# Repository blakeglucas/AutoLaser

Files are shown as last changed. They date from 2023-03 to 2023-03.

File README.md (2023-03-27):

# Auto Laser

An automatic laser pointer mover for your cat!

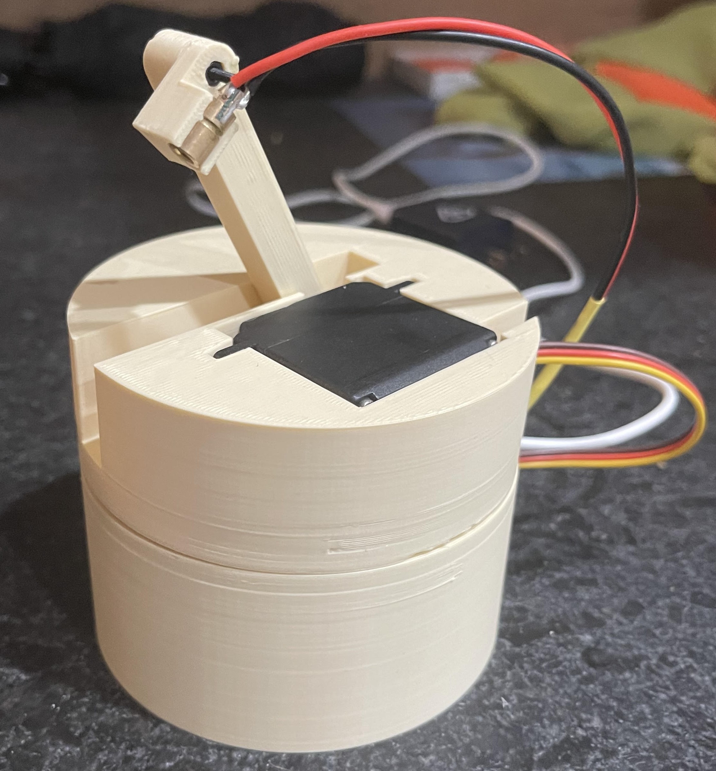
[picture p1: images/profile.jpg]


## Folders

### 3D

This folder contains the STL files for 3D printing and the FreeCAD source files for easy modification. Not every FreeCAD file has an associated STL because some are used as building blocks rather than as separate parts.

### Firmware

This folder contains the MicroPython firmware. This project was initially designed for the Pi Pico W, and the BaseMount part includes a corresponding mount, but you could modify it for use with another MicroPython compatible board (or just write your own firmware).

### PCB

This folder contains the design files for a Pi Pico (W) hat that makes connecting the laser and motors to the Pi Pico much easier. This part is not required.

## BOM

| Quantity | Part |
| ---| --- |
| 2 | TowerPro SG-5010 (or body-compatible) servo motors |
| 1 | Pi Pico W |
| 4 | M3x8 bolts |
| 4 | M3 nuts |
| 5 | M2x8 bolts |
| 5 | M2 nuts |
| 1 | Laser diode module |
| 2 | Longer wires for the laser module |
| 1 | Micro-USB cable and wall plug |
| Any | Cat |

> Servos: https://www.adafruit.com/product/155

> Laser Diodes: https://www.amazon.com/gp/product/B088PQQ9XV/

## Instructions

> If using a Pi Pico (W), be sure to flash MicroPython before starting. https://micropython.org/download/rp2-pico/

1. 3D print the STL files in the `3D` folder. Print plenty of extras of `ServoShaft` and `LaserArm`.
1. Connect your Pi Pico (W) to your computer and copy the Python files in the `Firmware` folder to your board, either via [Thonny](https://thonny.org/), [mpremote](https://docs.micropython.org/en/latest/reference/mpremote.html), or another way if you know one. After copying the files, disconnect your board from the computer.
1. (If using the PicoHat PCB) Solder the PicoHat to your Pi Pico (W).
1. Disassemble your servos and replace each drive shaft with the printed `ServoShaft` piece. It should be a drop-in replacement. Reassemble.
1. Attach the Pi Pico (W) to the `BaseMount` part using four of the M2 bolts and nuts. If you're using the PicoHat PCB, it's tricky to get the two by the micro-USB port, but it is doable.
1. Attach one of the servos to the `BaseMount` part using the M3 bolts and nuts.
1. (If necessary) De-solder the stock wires from the module and solder on two longer wires.
1. Snap the laser diode module into the `LaserHolder` part.
1. Attach the `LaserHolder` part to the `LaserArm` part using the remaining M2 bolt and nut.
1. Slide the `LaserArm` part onto the free servo's shaft at as close to a 90 degree angle as you can get.
1. Insert the free servo with the `LaserArm` attached into the `YMount` part.
1. Attach the now-assembled `YMount` part to `BaseMount`.
1. Slide the servo and laser wires through the slit on the back of `BaseMount` and attach them to your Pi Pico (W), either via the provided PicoHat or another method.
1. Connect your board to a power source. The servos will be driven to the zero position (50% duty), pause for five seconds, then begin the random laser movement.

## 3D Printing Instructions

> If you haven't tried the "Lightning" fill pattern in PrusaSlicer/SuperSlicer, give it a shot.

### BaseMount

Print top-face-down, using supports for only the counterbore screw holes on the face. Any infill, any layer height (0.2mm recommended).

### LaserArm

Print with the gear attachment hole facing up. Use support for only the counterbore screw hole. Sparse infill is fine, any layer height (18% and 0.2mm recommended, respectively).

### LaserHolder

Print the obvious orientation. No supports required. A finer layer height could be beneficial, but 0.2mm will work just fine.

### ServoShaft

If you have a printer with a 0.2-0.25mm nozzle, that is preferable, but a 0.4mm nozzle will work too. Add a support enforcer for the large negative area inside the gear, but support is not required for inside the smaller hole. 0.2mm layer height recommended, 100% infill for strength.

### YMount

Print the obvious orientation. Use support for the inset hole but not for inside the gear hole. Sparse infill, 0.2mm layer height recommended.

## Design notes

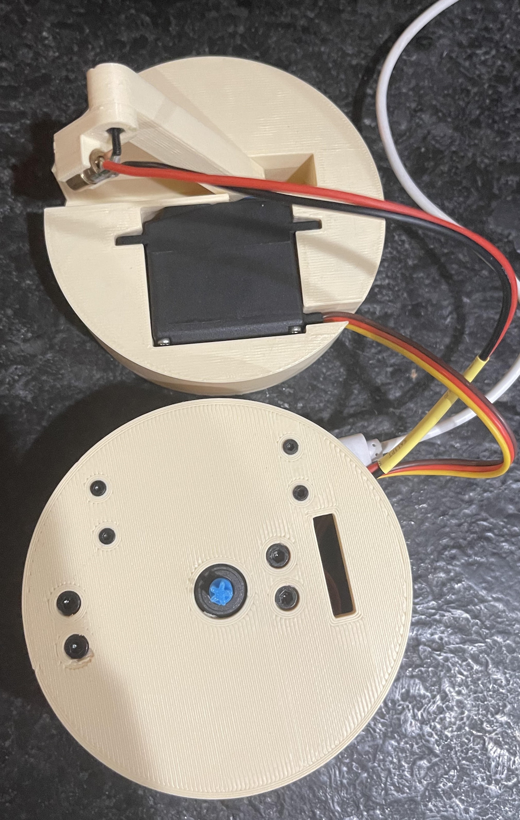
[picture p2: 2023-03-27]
images/top.jpg

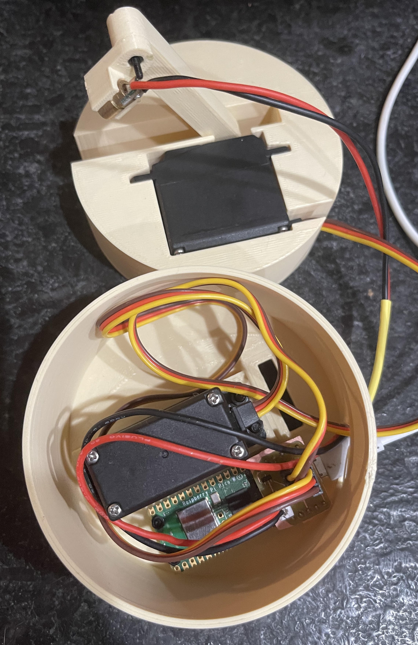
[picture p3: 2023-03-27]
images/inside.jpg

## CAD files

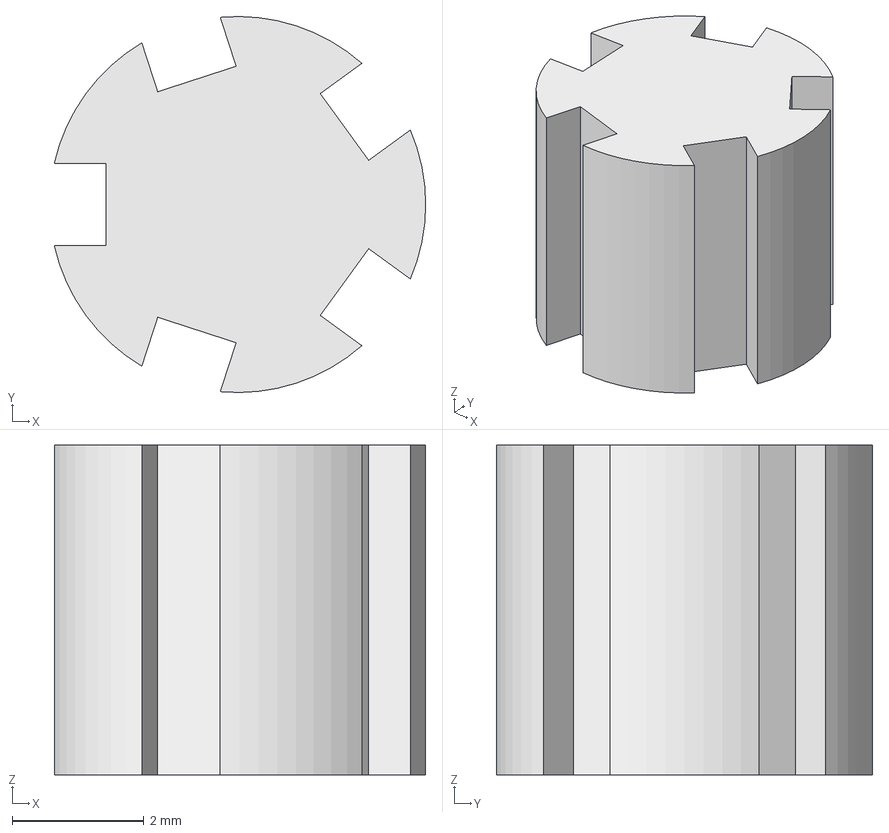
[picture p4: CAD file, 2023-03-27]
3D/ShaftConnector.FCStd
5.63 x 5.70 x 5.00 mm

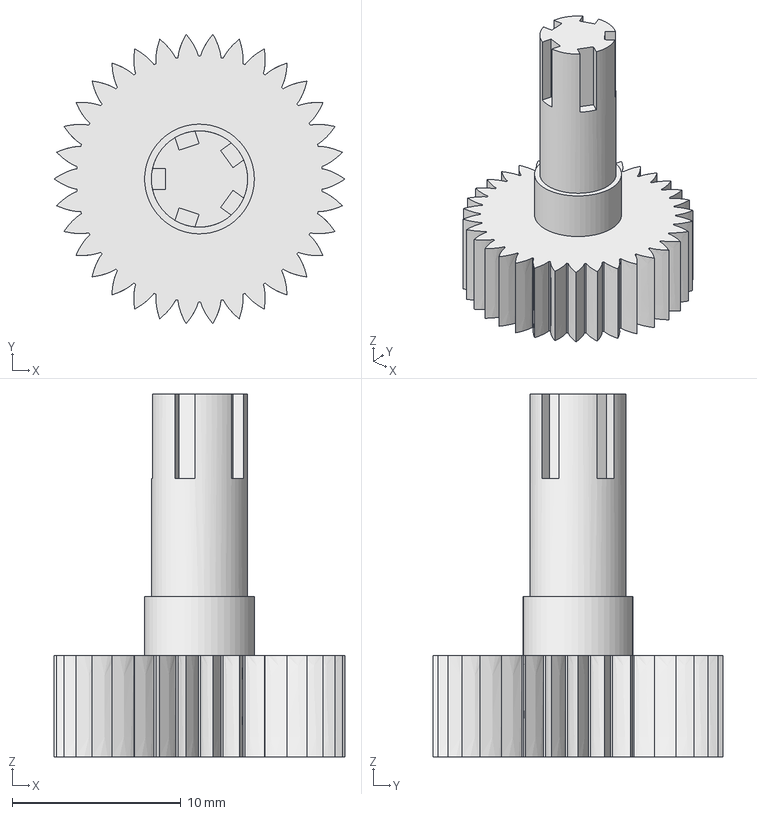
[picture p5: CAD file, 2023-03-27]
3D/ServoShaft.FCStd
17.2 x 17.1 x 21.5 mm

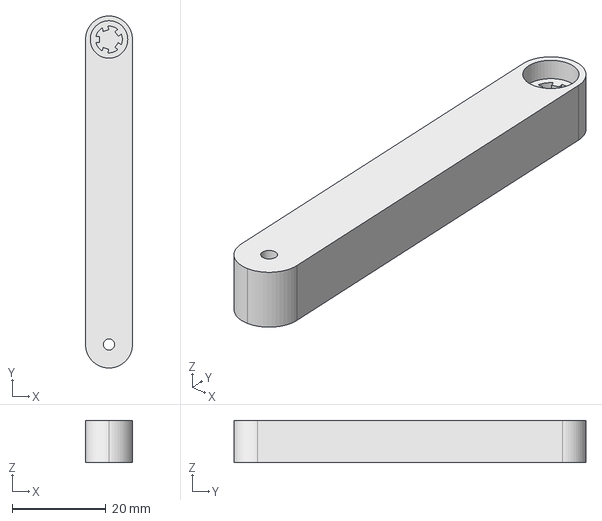
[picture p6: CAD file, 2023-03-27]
3D/LaserArm.FCStd
10.0 x 75.0 x 9.00 mm

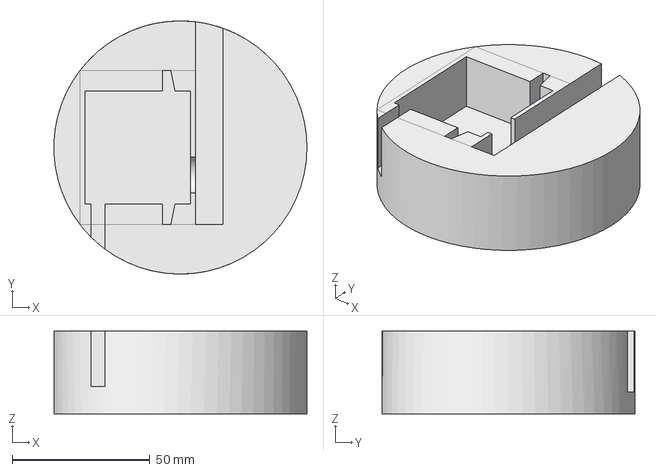
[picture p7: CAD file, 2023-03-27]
3D/YMount.FCStd
91.9 x 92.0 x 30.0 mm

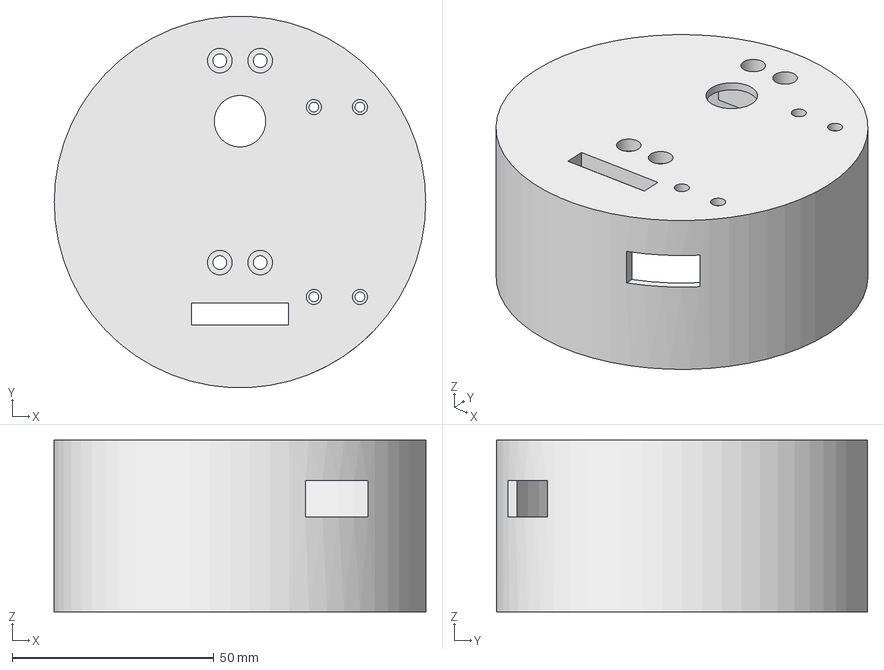
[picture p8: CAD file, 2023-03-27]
3D/BaseMount.FCStd
92.0 x 91.9 x 42.5 mm

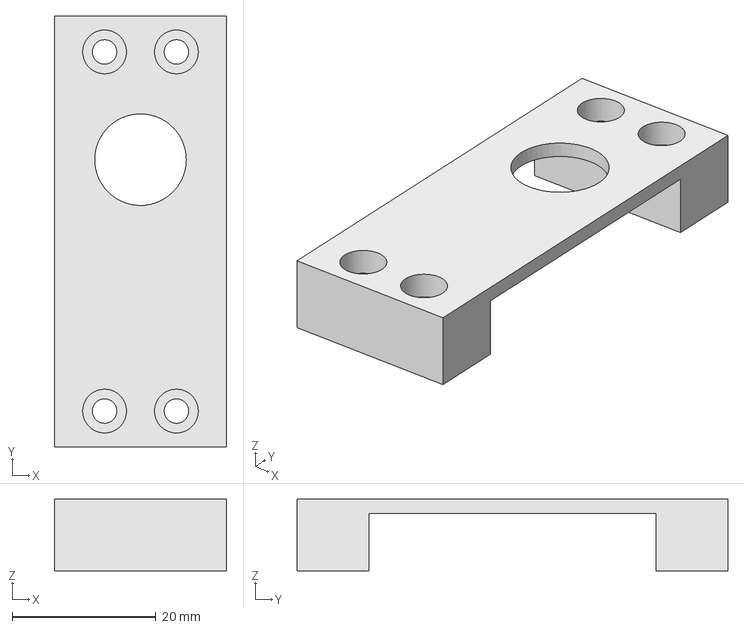
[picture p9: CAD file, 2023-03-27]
3D/ServoFaceMount.FCStd
24.0 x 60.0 x 10.0 mm

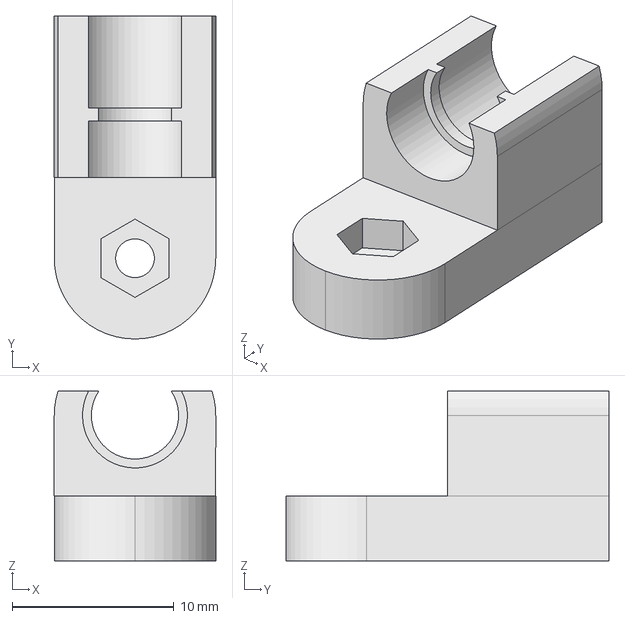
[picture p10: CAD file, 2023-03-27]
3D/LaserHolder.FCStd
10.0 x 20.0 x 10.5 mm

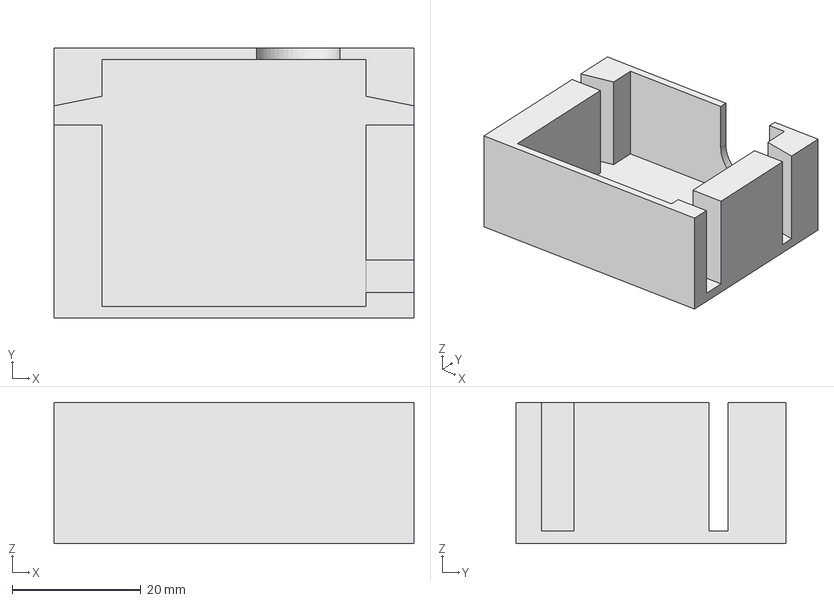
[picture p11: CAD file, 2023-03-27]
3D/InsertionMount.FCStd
56.0 x 42.0 x 22.0 mm

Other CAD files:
3D/BaseMount.stl
3D/LaserArm.stl
3D/LaserHolder.stl
3D/ServoShaft.stl
3D/YMount.stl

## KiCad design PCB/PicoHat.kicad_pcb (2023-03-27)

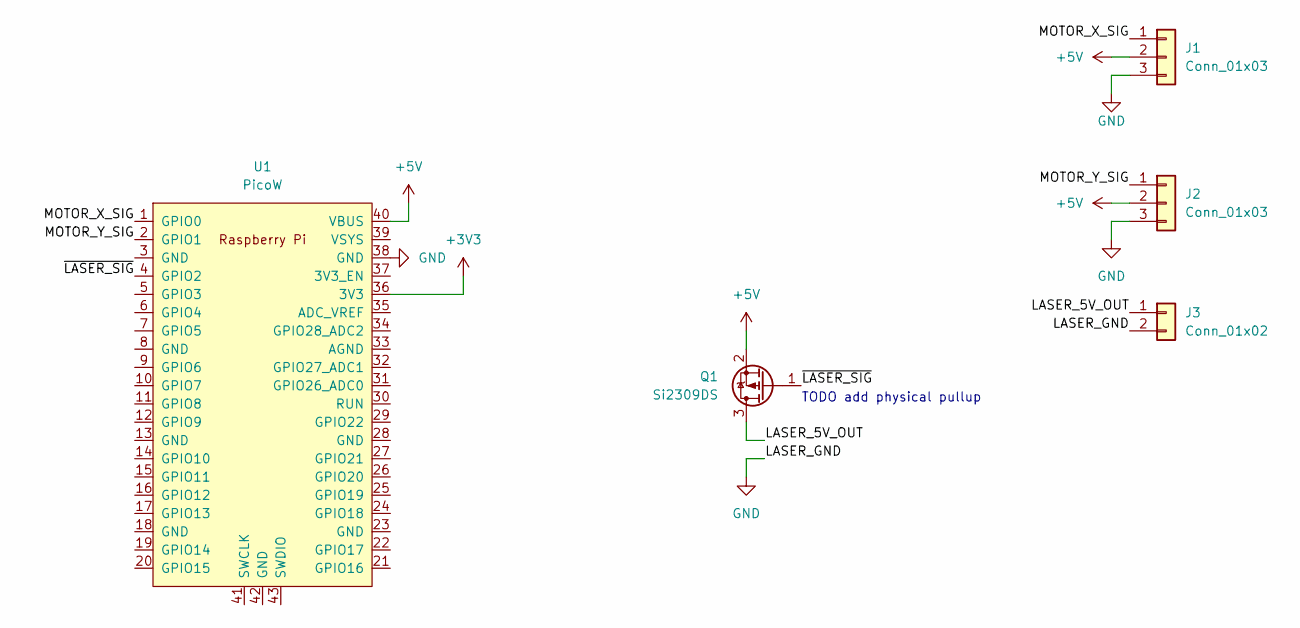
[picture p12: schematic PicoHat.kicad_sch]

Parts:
J1, J2: Conn_01x03; PinHeader_1x03_P2.54mm_Vertical
J3: Conn_01x02; PinSocket_1x02_P2.00mm_Vertical
Q1: Si2309DS; SOT-23
U1: PicoW; RPi_PicoW_SMD_TH

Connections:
+3V3: U1.36 (3V3)
+5V: J1.2, J2.2, Q1.2 (S), U1.40 (VBUS)
/LASER_5V_OUT: J3.1, Q1.3 (D)
/MOTOR_X_SIG: J1.1, U1.1 (GPIO0)
/MOTOR_Y_SIG: J2.1, U1.2 (GPIO1)
/~LASER_SIG: Q1.1 (G), U1.4 (GPIO2)
GND: J1.3, J2.3, J3.2, U1.38 (GND)

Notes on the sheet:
TODO add physical pullup

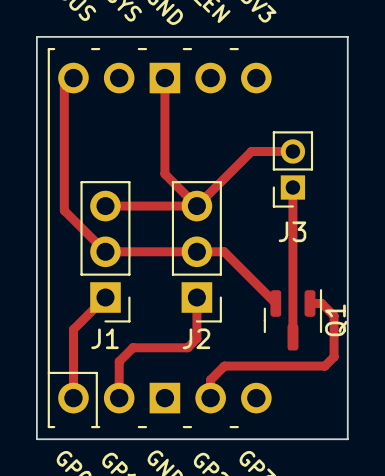
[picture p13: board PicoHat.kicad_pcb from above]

Board: 2 copper layers, 17.3 x 22.4 mm, 5 parts (0 on the bottom side), 6 nets.

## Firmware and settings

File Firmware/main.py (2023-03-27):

from Laser import Laser
from random import randrange
from ServoDriver import ServoDriver
import time
import uasyncio

# Y Driver max range: 10-90
# Y Driver effective range: 50-75 !! this depends on LaserHolder attachment angle and your play space
X_RANGE = (0, 100)
Y_RANGE = (60, 90)

async def main():
    lsr = Laser()
    lsr.off()
    x_drv = ServoDriver(0, X_RANGE)
    y_drv = ServoDriver(1, Y_RANGE)
    time.sleep(5)
    lsr.on()
    while True:
        x_pos = randrange(*X_RANGE)
        y_pos = randrange(*Y_RANGE)
        x_time = randrange(1, 5)
        delay = randrange(100, 1000)
        x_task = uasyncio.create_task(x_drv.move(x_pos, x_time))
        y_task = uasyncio.create_task(y_drv.move(y_pos, x_time))
        await uasyncio.gather(x_task, y_task)
        print(x_pos, y_pos, x_time, delay)
        time.sleep(delay / 1000.0)

uasyncio.run(main())

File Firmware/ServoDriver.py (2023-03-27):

from machine import Pin, PWM
import uasyncio

SERVO_MIN_DUTY = 0.2
SERVO_MAX_DUTY = 0.95
SERVO_FREQ = 400
SERVO_DUTY_DELTA = SERVO_MAX_DUTY - SERVO_MIN_DUTY
SERVO_ZERO_DUTY = SERVO_DUTY_DELTA / 2.0
INT_U16_MAX = (1 << 16) - 1


class ServoDriver(object):

    pct_max: float = 100
    pct_min: float = 0
    ctrl_pwm: PWM

    _cur_pct: float

    def __init__(self, pin: int, pct_range: tuple[float, float] | None = None):
        if pct_range:
            self.pct_max = max(pct_range)
            self.pct_min = min(pct_range)
        self.ctrl_pwm = PWM(Pin(pin, mode=Pin.OUT))
        self.ctrl_pwm.freq(SERVO_FREQ)
        # Home over time--instant torque breaks ServoShaft frequently
        uasyncio.run_until_complete(self.move(50, 3))

    def duty_pct(self, pct: float):
        if pct > self.pct_max:
            pct = self.pct_max
        elif pct < self.pct_min:
            pct = self.pct_min
        self._cur_pct = pct
        factor = (SERVO_DUTY_DELTA * pct / 100.0) + SERVO_MIN_DUTY
        self.ctrl_pwm.duty_u16(int(INT_U16_MAX * factor))

    async def move(self, target_pct: float, time_s: float, timestep=0.01):
        # Enforce here as well to keep timing consistent
        if target_pct < self.pct_min:
            target_pct = self.pct_min
        elif target_pct > self.pct_max:
            target_pct = self.pct_max
        delta_target = target_pct - self._cur_pct
        step_pct = delta_target * timestep / time_s
        time_ctr = 0
        while time_ctr <= time_s:
            self.duty_pct(self._cur_pct + step_pct)
            await uasyncio.sleep(timestep)
            time_ctr += timestep

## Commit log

2023-03-27 Intial commit
    [BaseMount.FCStd, BaseMount.stl, InsertionMount.FCStd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]
2023-03-27 ServoShaft v2, removed instant snap to home in ServoDriver
    [LaserArm.FCStd, LaserArm.stl, ServoShaft.FCStd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]
